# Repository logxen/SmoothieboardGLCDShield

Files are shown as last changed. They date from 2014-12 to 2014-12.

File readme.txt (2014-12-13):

Smoothieboard GLCD Shield

Licensed under the CERN Open Hardware License version 1.2

This simple pcb makes connecting the common Reprap Discount GLCD Screen to a Smoothieboard very easy. It has an optional footprint for a 5V regulator to make sure the screen gets enough power. Information on how to configure Smoothieware for use with a display panel can be found here: http://smoothieware.org/panel

The only truly required component other than the connectors is a schottky diode such as SK310A.

Bill of Materials:

2x SK310A (or similar) SMA schottky diodes to protect voltage inputs from reverse flow
2x 0.1uF 0603 capacitors
1x R78E5.0-0.5 switching voltage regulator
2x 2x5 0.1" shrouded male header
1x 1x3 0.1" male breakaway header
1x 0.1" jumper
2x 2x3 0.1" female header
2x 1x3 0.1" female header
1x 1x4 0.1" female header
1x 1x5 0.1" female header
1x 1x6 0.1" stacking female header (or just a 1x3 female header)

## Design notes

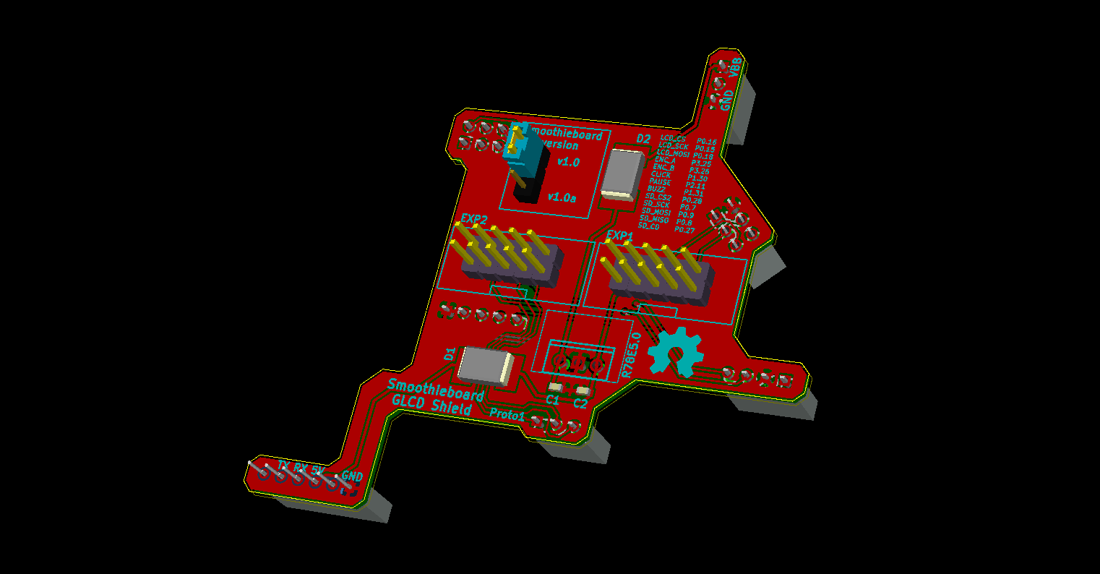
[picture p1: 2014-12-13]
SmoothieGLCDShield-Proto1-Pre1.png

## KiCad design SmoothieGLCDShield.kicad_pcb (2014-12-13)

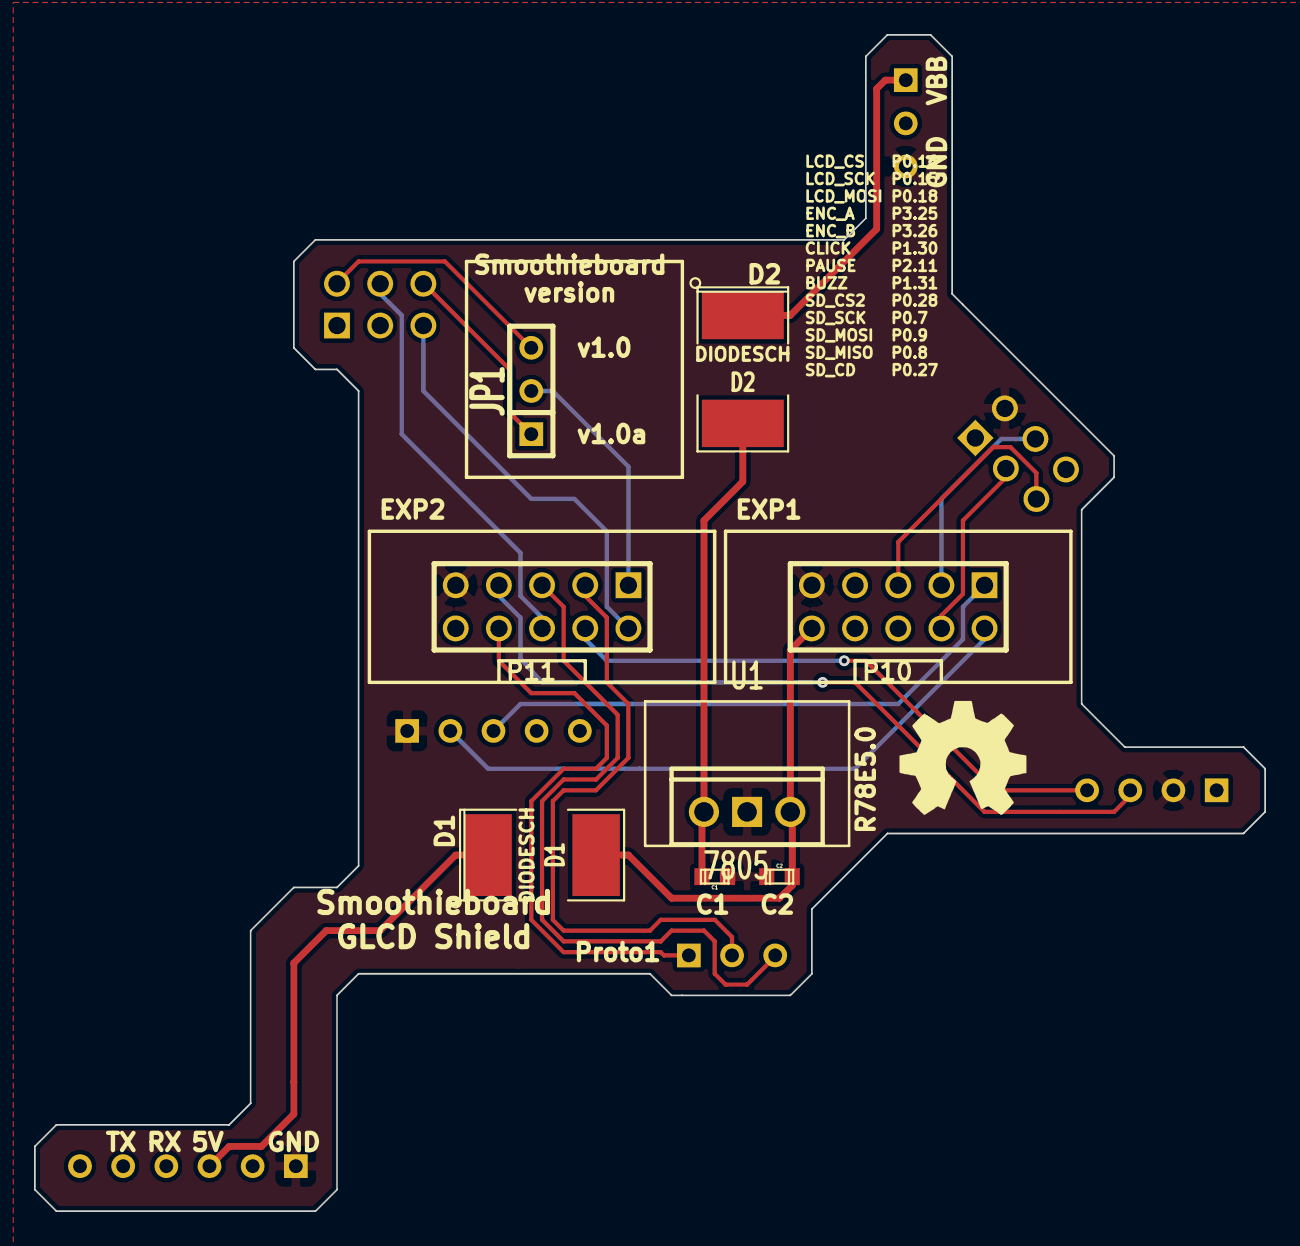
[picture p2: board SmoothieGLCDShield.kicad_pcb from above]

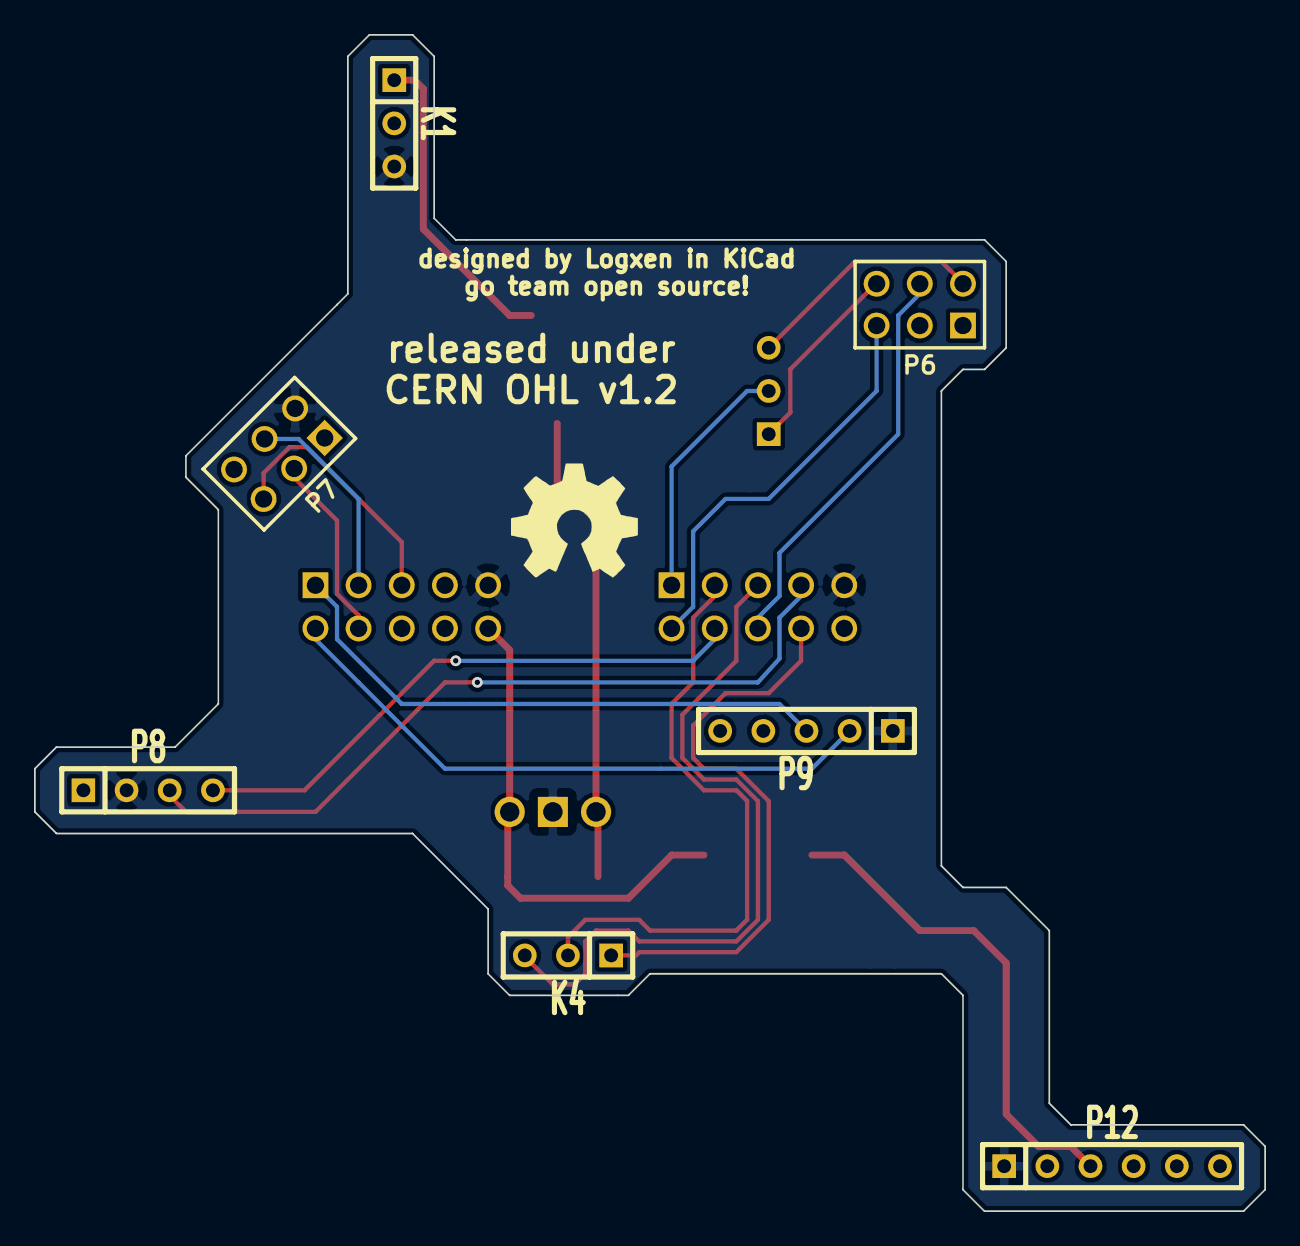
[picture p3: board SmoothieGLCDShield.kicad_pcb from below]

Board: 2 copper layers, 72.4 x 69.2 mm, 17 parts (8 on the bottom side), 20 nets.

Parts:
C1, C2: C; c_0603
D1, D2: DIODESCH; SM2112L
JP1: JUMPER3; SIL-3
K1, K4: CONN_3; SIL-3
P6, P7: CONN_3X2; pin_array_3x2_pin1_REV
P8: CONN_4; SIL-4
P9: CONN_5; SIL-5
P10, P11: CONN_5X2; PIN_ARRAY_5x2
P12: CONN_6; SIL-6
U1: 7805; R-78E05
VAL: REF; OSHW-LOGO_SMALL
VAL#2: REF; OSHW-LOGO_SMALL

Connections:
/5V: C2.1, D1.2, P10.10, U1.VO
/5VIN: D1.1, P12.3
/GND: C1.2, C2.2, K1.3, P7.2, P8.2, P9.1, P10.9, P11.9, P12.1, U1.GND
/LCD_MOSI: P7.4, P10.3
/LCD_SCK: P7.5, P10.5
/LCD_SSEL: P7.3, P10.4
/P1.30: P9.2, P10.2
/P1.31: P9.3, P10.1
/P2.11: K4.1, P11.8
/P3.25: K4.3, P11.5
/P3.26: K4.2, P11.3
/SD_CD: P8.3, P11.7
/SD_MISO: JP1.2, P11.1
/SD_MISO_NEW: JP1.1, P6.6
/SD_MISO_OLD: JP1.3, P6.2
/SD_MOSI: P6.4, P11.6
/SD_SCK: P6.5, P11.2
/SD_SSEL2: P8.4, P11.4
/VBB: D2.1, K1.1
/VBB_REG: C1.1, D2.2, U1.VI

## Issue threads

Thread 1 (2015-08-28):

Add SD card connector pinout

arthurwolf, 2015-08-28:
Some users want external SD cards that are not on the panel itself ( I'll be using that in the Laser cutter and Vinyl cutter Smoothie kits ).
It'd be nice to have a connectors to easily connect those.
Also a SD card ( not microsd ) breakout that can be connected to this with a wire would be nice.

Cheers :)

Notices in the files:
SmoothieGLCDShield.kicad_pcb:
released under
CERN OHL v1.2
